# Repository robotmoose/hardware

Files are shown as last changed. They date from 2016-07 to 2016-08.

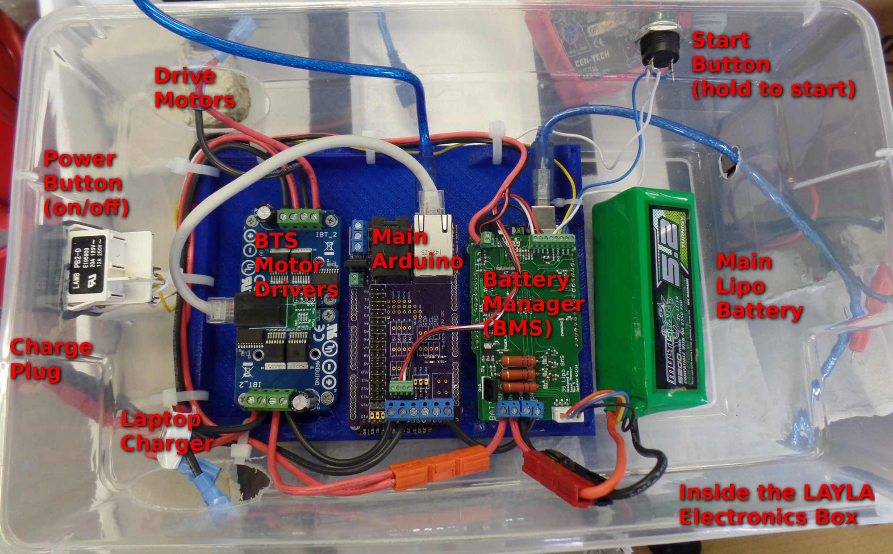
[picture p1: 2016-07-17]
layla/hardware/layla_electronics_box.jpg

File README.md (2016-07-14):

# RobotMoose Web Robotics System Hardware



Several robotics platforms are being developed specifically for use with the RobotMoose Web Robotics System. This repository stores files related to the hardware developed for these systems.
* The **layla**, **quizbot**, and **roomba** folders contain firmware and 3d models of parts and assemblies for those respective systems.
* The **sensors** folder contains files for subsystems being developed to expand the functionality of our robotics platforms.

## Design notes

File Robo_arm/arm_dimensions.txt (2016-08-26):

//Arm dimensions

//from shoulder/ball joint to forearm
first length = 8 inches or (8in*2.5cm = 20cm)   215mm 

//forearm
9 inches or (9in * 2.5cm = 22.5cm) 200mm

//wrist

//finger
2inches on each side of the corner or 4 inches total = 5cm = 50mm

35mm for bottom 
50mm for top including tip
30mm w/o tip

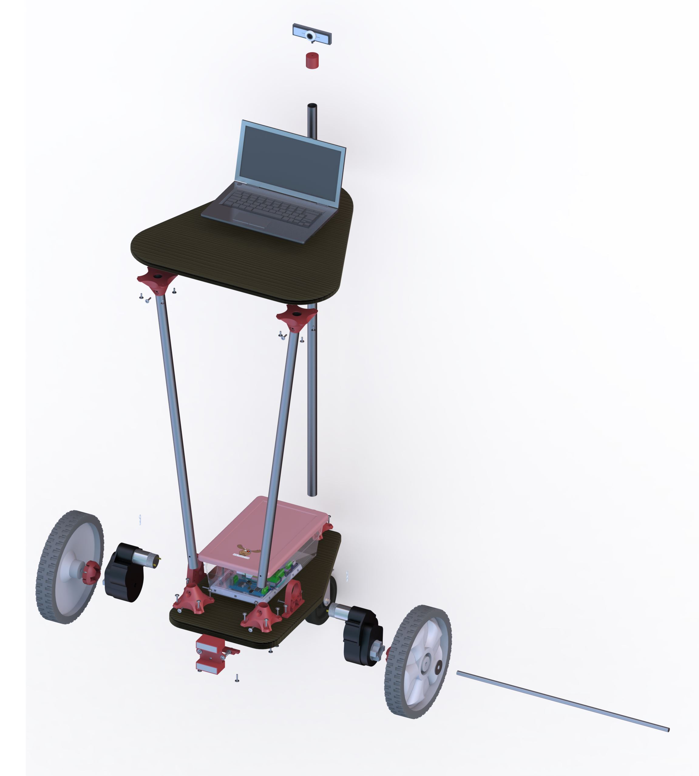
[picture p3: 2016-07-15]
layla/SolidWorks/Renders, Animations, & Schematics/Layla_Exploded_Isometric.jpg

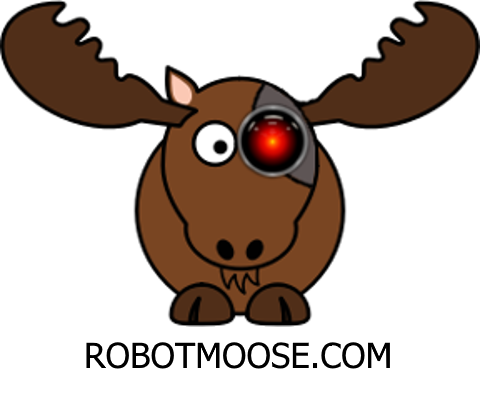
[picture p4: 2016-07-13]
layla/SolidWorks/electronics_box/moose_sticker.png

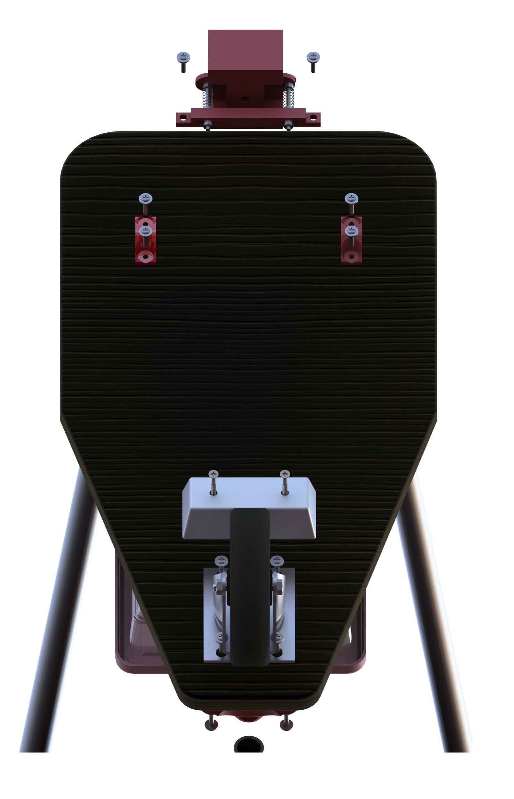
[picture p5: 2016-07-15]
layla/SolidWorks/Renders, Animations, & Schematics/Layla_Explode_Bottom.jpg

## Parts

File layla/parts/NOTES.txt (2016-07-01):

Bottom plywood: 
	3/4 inch thick
	10 inches wide
	22 inches deep
	
Top plywood: 
	5mm thick, approx
	22 inches wide (must be as wide as wheels, to make driving easier)
	22 inches deep
	Work surface sits 38 inches off the ground

Electrical Metallic Tubing (EMT), 3/4 inch (nominal), 23.5mm (actual)
	1x 44 inch long upright for camera
	2x 32 inch long slanted uprights; slant angle is 11 degrees from vertical

Axle:
	22.75 inch 3/8" (or 7/16" if available) steel axle; both ends cross-drilled for retaining clips.

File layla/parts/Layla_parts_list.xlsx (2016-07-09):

part # | part | dimension | quantity | source | price
965207 | drive wheel | 11in | 2 | home depot | $21.98
235574 | caster wheel |  | 1 | lowes | $11.97
90075K145 | axle | 7/16 x ? |  | mcmaster | $7.01
SAGI9951KWN | motor/gears |  | 1 | tiger imports | $22.00
154280 | plywood base | 20" x 12" | 1 | lowes | $14.93
154277 | plywood top | 22" x 22" | 1 | lowes | $13.27
 | electronics tray |  | 1 | RobotMoose | $91.16
16428012 | shoe box |  | 1* | walmart | $8.69
B00JTBMD7E | Arduino Mega |  | 1* | amazon | $18.99
B008GRTSV6 | Arduino Uno |  | 1* | amazon | $15.99
B00WSN98DC | BTS7960 Motor control |  | 1* | amazon | $13.59
912700001-0 | Battery | 3S 5.2aH | 1* | hobby king | $16.99
 | BMS UNO shield |  | 1* | RobotMoose | $74.25
 | Mainboard Mega Shield |  | 1* | RobotMoose | $165.41
 | BTS dual adapter |  | 1* | RobotMoose
B00852KMLC | LAN cable | 12" | 1* | amazon | $4.98
B00NH11KIK | usb cable | 6' | 1* | amazon | $4.99
B00NAY1T80 | start button |  | 1* | amazon | $5.99
PB241D212Z02T-ND | E-stop Button |  | 1* | digikey | $2.75
72713 | Metal upright legs |  | 1 | lowes | $3.99
 | printed wheel adapters |  |  | robotMoose download | $22.70
 | printed rear volcanoes |  |  | robotMoose download
 | printed front volcanoes |  |  | robotMoose download
 | printed webcam holder |  |  | robotMoose download
B00GZB8D0M | laptop |  | 1 | amazon | $139.29
B0080CE5M4 | webcam |  | 1 | amazon | $30.69
205142852 | volcano-base screw | #8 x 3/4 | partial box | home depot | $5.64
205142871 | volcano-top screw | #8 x 1/2 | partial box | home depot | $5.64
122235 | leg screws |  | partial box | lowes | $6.14
 |  |  |  |  | $751.01
*included with electronics box
download link:
https://github.com/robotmoose/robotmoose/tree/master/layla/parts

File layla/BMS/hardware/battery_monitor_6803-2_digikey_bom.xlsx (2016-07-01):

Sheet: Sheet1
Qty | Value | Package | Reference | digikey #
3 |  | LED-0603 | LED1, LED2, LED3 | 475-2512-1-ND
3 | 0.1uF | 0603-CAP | C1, C2, C3 | 490-1532-1-ND
5 | 100 | 0603-RES | R4, R5, R6, R7, R8 | RHM100CGCT-ND
1 | 100k | 0603-RES | R11 | RHM100KCGCT-ND
3 | 1Meg | 0603-RES | R22, R23, R24 | RHM1MCGCT-ND
4 | 1uF | 0603-CAP | C4, C5, C6, C7 | 490-10487-1-ND
3 | 3.3k | 0603-RES | R1, R2, R3 | RHM3.3KCGCT-ND
10 | 4.7k | 0603-RES | R9, R10, R12, R13, R14, R15, R19, R20, R21, R25 | RHM4.7KCGCT-ND
3 | 470 | 0603-RES | R16, R17, R18 | RHM470CGCT-ND
1 | LTC6803-2 | FSOP-44 | U$5 | LTC6803IG-2#PBF-ND
4 | MOSFET-NCHANNELBSS138 | SOT23 | Q2, Q6, Q7, Q8 | SSM3K333RLF(TCT-ND
4 | MOSFET-PCHANNELIRLML2244 | SOT23-3 | Q1, Q3, Q4, Q5 | SSM3J334RLFCT-ND
3 | PDZ7.5B | SOD-323 | DZ1, DZ2, DZ3 | MM3Z7V5ST1GOSCT-ND
1 | PMLL41SOD80C | SOD80C | D2 | LS4148-GS18CT-ND
1 | PMOS_AO4435 | SOIC8 | Q9 | BSO613SPV GCT-ND
3 | RESISTOR-POWER-3W | RESISTOR-3W | U$1, U$2, U$3 | PPC20W-3JTB-ND
2 | SCREW_TERMINAL_2 | SCREW_TERMINAL_2 | I2C, RELAYS, THERM | A98333-ND
1 | SCREW_TERMINAL_3 | SCREW_TERMINAL_3 | U$4 | A98334-ND
1 |  | through-hole | cell connector | 455-2237-ND

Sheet: battery_monitor_6803-2
Qty;"Value";"Device";"Package";"Parts";"Description";"PROD_ID";"VALUE";
3;"";"LED0603";"LED-0603";"LED1 | LED2 | LED3";"LEDs";"";"";
5;"";"SOLDERJUMPER_2WAYS";"SJ_3";"A0 | A1 | A2 | A3 | TOS";"Solder Jumper";"";"";
3;"0.1uF";"0.1UF-100V-10%(0603)";"0603-CAP";"C1 | C2 | C3";"CAP-08390";"CAP-08390";"0.1uF";
5;"100";"3.3KOHM1/10W1%(0603)";"0603-RES";"R4 | R5 | R6 | R7 | R8";"RES-07851";"RES-07851";"";
1;"100k";"3.3KOHM1/10W1%(0603)";"0603-RES";"R11";"RES-07851";"RES-07851";"";
3;"1Meg";"3.3KOHM1/10W1%(0603)";"0603-RES";"R22 | R23 | R24";"RES-07851";"RES-07851";"";
4;"1uF";"0.1UF-100V-10%(0603)";"0603-CAP";"C4 | C5 | C6 | C7";"CAP-08390";"CAP-08390";"0.1uF";
3;"3.3k";"3.3KOHM1/10W1%(0603)";"0603-RES";"R1 | R2 | R3";"RES-07851";"RES-07851";"";
10;"4.7k";"3.3KOHM1/10W1%(0603)";"0603-RES";"R9 | R10 | R12 | R13 | R14 | R15 | R19 | R20 | R21 | R25";"RES-07851";"RES-07851";"";
3;"470";"3.3KOHM1/10W1%(0603)";"0603-RES";"R16 | R17 | R18";"RES-07851";"RES-07851";"";
1;"ARDUINO_R3_SHIELD";"ARDUINO_R3_SHIELD";"UNO_R3_SHIELD";"U$8";"Shield form compatible with the Arduino Uno R3.";"";"";
1;"LTC6803-2";"LTC6803-2";"FSOP-44";"U$5";"";"";"";
4;"MOSFET-NCHANNELBSS138";"MOSFET-NCHANNELBSS138";"SOT23";"Q2 | Q6 | Q7 | Q8";"Common NMOSFET Parts";"TRANS-00830";"";
4;"MOSFET-PCHANNELIRLML2244";"MOSFET-PCHANNELIRLML2244";"SOT23-3";"Q1 | Q3 | Q4 | Q5";"Generic PMOSFET";"TRANS-11153";"";
3;"PDZ7.5B";"DIODE-ZENER-BZT52";"SOD-323";"DZ1 | DZ2 | DZ3";"Zener Diode";"";"";
1;"PMLL41SOD80C";"PMLL41SOD80C";"SOD80C";"D2";"High-speed diodes";"";"";
1;"PMOS_AO4435";"PMOS_AO4435";"SOIC8";"Q9";"";"";"";
3;"RESISTOR-POWER-3W";"RESISTOR-POWER-3W";"RESISTOR-3W";"U$1 | U$2 | U$3";"PR03 series .205" dia x .657" L";"";"";
3;"SCREW_TERMINAL_2";"SCREW_TERMINAL_2";"SCREW_TERMINAL_2";"I2C | RELAYS | THERM";"";"";"";
2;"SCREW_TERMINAL_4";"SCREW_TERMINAL_4";"SCREW_TERMINAL_4";"CELL_CONNECTION | U$4";"";"";"";

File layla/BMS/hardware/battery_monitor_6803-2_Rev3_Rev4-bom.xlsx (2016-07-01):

Order list for /home/clayauld/Documents/Seafile/UAF/ITEST/ITEST Eagle/BMS/battery_monitor_6803-2_Rev4.sch
Exported from EAGLE with DesignLink
Parts for 3 boards
Quantity | Value | Package | Newark Order code | Digikey order code | Manufacturer | Manuf. Code | Reference | Availability | Price (from) | Description
9 | 0.1uF | 0603-CAP | 01H6821 | 490-1532-1-ND | AVX CORPORATION | 0603YG104ZAT2A | C1, C2, C3 | 48000 | 0.016 | AVX - 0603YG104ZAT2A - CAPACITOR | CERAMIC | 0.1UF | 16V | Y5V | 80% |  | -20% | 603 | FULL REEL
12 | 1uF | 0603-CAP | 04X3184 | 490-10487-1-ND |  | C0603X5R0J105M030BC | C4, C5, C6, C7 | 35812 | 0.086 | TDK - C0603X5R0J105M030BC - CERAMIC CAPACITOR | 1UF | 6.3V | X5R | 201
3 | SCREW_TERMINAL_4 | SCREW_TERMINAL_4 | 12H8388 | A98335-ND | TYCO ELECTRONICS | 282834-4 | Charger/Battery+ | 5317 | 1.02 | TE CONNECTIVITY / BUCHANAN - 282834-4 - TERMINAL BLOCK | PCB | 4 POSITION | 30-16AWG
3 | PMLL41SOD80C | SOD80C | 18C6408 | LS4148-GS18CT-ND | FAIRCHILD SEMICONDUCTOR | FDLL4148 | D2 | 8482 | 0.015 | FAIRCHILD SEMICONDUCTOR - FDLL4148 - SMALL SIGNAL DIODE 100V 200mA LL-34
9 | PDZ7.5B | SOD-323 | 04X4941 | MM3Z7V5ST1GOSCT-ND |  | PDZ7.5B | DZ1, DZ2, DZ3 | 115 | 224 | 0.021 | NXP - PDZ7.5B | 115 - DIODE | ZENER | 7.5V | 400MW | SOD-323-2
9 | SCREW_TERMINAL_2 | SCREW_TERMINAL_2 | 12H8386 | A98333-ND | TYCO ELECTRONICS | 282834-2 | I2C, ESTOP, THERM | 2599 | 0.502 | TE CONNECTIVITY / BUCHANAN - 282834-2 - TERMINAL BLOCK | PCB | 2 POSITION | 30-16AWG
9 |  | LED-0603 | 95W3795 | 732-4978-1-ND |  | 150060RS75000 | LED1, LED2, LED3 | 20 | 0.101 | WURTH ELEKTRONIK - 150060RS75000 - LED | 603 | RED | 250MCD | 625NM
12 | MOSFET-PCHANNELIRLML2244 | SOT23-3 | 40X8697 | SSM3J334RLFCT-ND |  | SI2369DS-T1-GE3 | Q1, Q3, Q4, Q5 | 0 | 0.126 | VISHAY SILICONIX - SI2369DS-T1-GE3 - MOSFET | P CH | -30V | -7.6A | SOT-23-3
12 | MOSFET-NCHANNELBSS138 | SOT23 | 52R2613 | SSM3K333RLF(TCT-ND |  | IRLML0030TRPBF | Q2, Q6, Q7, Q8 | 2952 | 0.169 | INTERNATIONAL RECTIFIER - IRLML0030TRPBF - N CHANNEL MOSFET | 30V | 5.3A | SOT-23
3 | PMOS_AO4435 | SOIC8 | 16P3885 | BSO613SPV GCT-ND |  | SI9407BDY-T1-GE3 | Q9 | 1742 | 0.56 | VISHAY SILICONIX - SI9407BDY-T1-GE3 - P CHANNEL MOSFET | -60V | 4.7A | SOIC
3 | IRF9530 | TO220BV | 14T4215 | 497-2729-5-ND |  | NTE2383 | Q10 | 64 | 8.61 | NTE ELECTRONICS - NTE2383 - MOSFET | P CHANNEL | 100V | 10.5A | TO-220-3
9 | 3.3k | 0603-RES | 52K8368 | RHM3.3KCGCT-ND | VISHAY/DALE | CRCW06033K00FKEA | R1, R2, R3 | 3110 | 0.009 | VISHAY DALE - CRCW06033K00FKEA - THICK FILM RESISTOR | 3KOHM | 100mW | 1%
15 | 100 | 0603-RES | 05X8794 | RHM100CGCT-ND |  | ERJ-1GNF1000C | R4, R5, R6, R7, R8 | 20035 | 0.008 | PANASONIC ELECTRONIC COMPONENTS - ERJ-1GNF1000C - THICK FILM RESISTOR | 100 OHM | 1% | 201
30 | 4.7k | 0603-RES | 52K8494 | RHM4.7KCGCT-ND | VISHAY/DALE | CRCW06034K70FKEA | R9, R10, R12, R13, R14, R15, R19, R20, R21, R25 | 6964 | 0.003 | VISHAY DALE - CRCW06034K70FKEA - THICK FILM RESISTOR | 4.7KOHM | 100mW | 1%
3 | 100k | 0603-RES | 39K0075 | RHM100KCGCT-ND | FARNELL | MC0063W06035100K | R11 | 4003 | 0.011 | MULTICOMP - MC0063W06035100K - THICK FILM RESISTOR | 100KOHM | 63mW | 5%
9 | 470 | 0603-RES | 05X8640 | RHM470CGCT-ND |  | ERJ-P03F4700V | R16, R17, R18 | 4890 | 0.071 | PANASONIC ELECTRONIC COMPONENTS - ERJ-P03F4700V - THICK FILM RESISTOR | 470 OHM | 1% | 603
12 | 1Meg | 0603-RES | 64R5311 | RHM1MCGCT-ND |  | ERJ-3EKF1004V | R22, R23, R24, R26 | 2513 | 0.003 | PANASONIC ELECTRONIC COMPONENTS - ERJ-3EKF1004V - THICK FILM RESISTOR | 1MOHM | 100mW | 1%
9 | RESISTOR-POWER-3W | RESISTOR-3W | 52W7905 | PPC20W-3JCT-ND |  | ERG-3SJ200 | U$1, U$2, U$3 | 1214 | 0.099 | PANASONIC ELECTRONIC COMPONENTS - ERG-3SJ200 - RESISTOR | 20 OHM | 3W | 5% | AXIAL
3 | LTC6803-2 | FSOP-44 | unknown | LTC6803IG-2#PBF-ND |  |  | U$5 |  |  |  |  |  |  |  |  | 1 | LTC6803-2 | FSOP-44 | unknown | LTC6803IG-2#PBF-ND
3 | TACTILE-SWITCH-7914G | 7914G | 05B2757 | 7914G-000ECT-ND | BOURNS | INC. | U$7 | 7914G-1-000E | 338 | 0.465 | BOURNS - 7914G-1-000E - PUSHBUTTON | SPST-NO | 100MA | SMDGULLWING
3 | 3 cell jst connector | Jst-3-cell | 37K9958 | 455-2237-ND |  |  | Cell connection

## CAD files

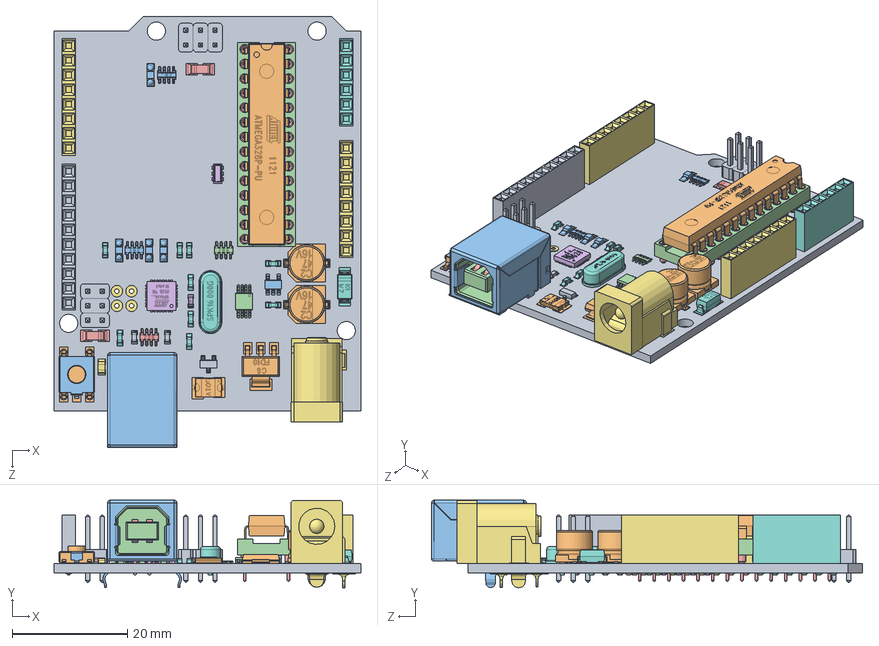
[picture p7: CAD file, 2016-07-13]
layla/SolidWorks/electronics_box/arduino uno.SLDASM
53.3 x 15.2 x 74.9 mm
unoboard blue
47uf CAP Dcase x 2
USB SHELL
USB core
usb top contact x 2
usb btm contact x 2
power jack
crystal
2pin_header__02 x 6
nano - reg
led x 4
dip28
dip socket pin x 28
atmega16u2
8 PORT HEADER x 2
6 PORT HEADER
10 PORT HEADER
ATMEL328P
102 RESISTOR PACK x 2
103 RESISTOR PACK
220 RESISTOR PACK
16mhz crystal - measured
PADS001
603 cap on pad x 9
ssot3
mf-msmf050-2
lmv358
lp2985dgkr
cd1206 diode x 2
603 resistor
blm21
m7 diode
MLC0603 x 2
RESET CORE
RESET

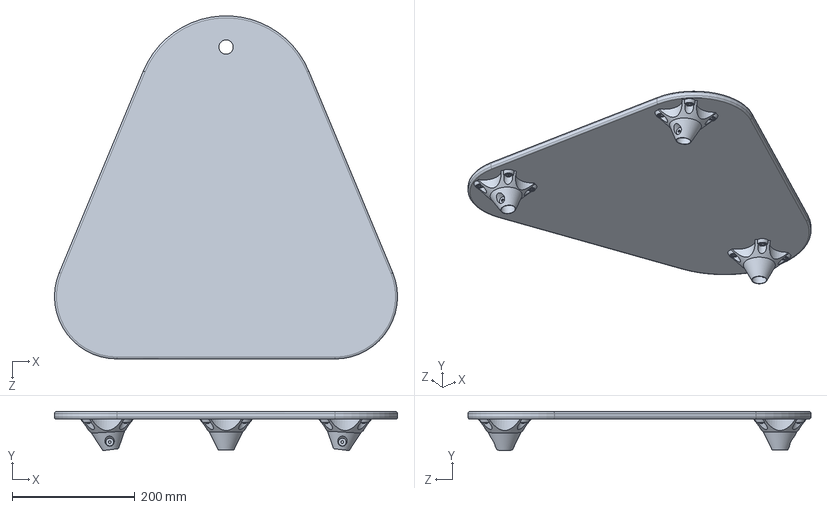
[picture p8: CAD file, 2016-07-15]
layla/SolidWorks/Layla_Top_Full.SLDPRT
558.8 x 63.9 x 558.6 mm

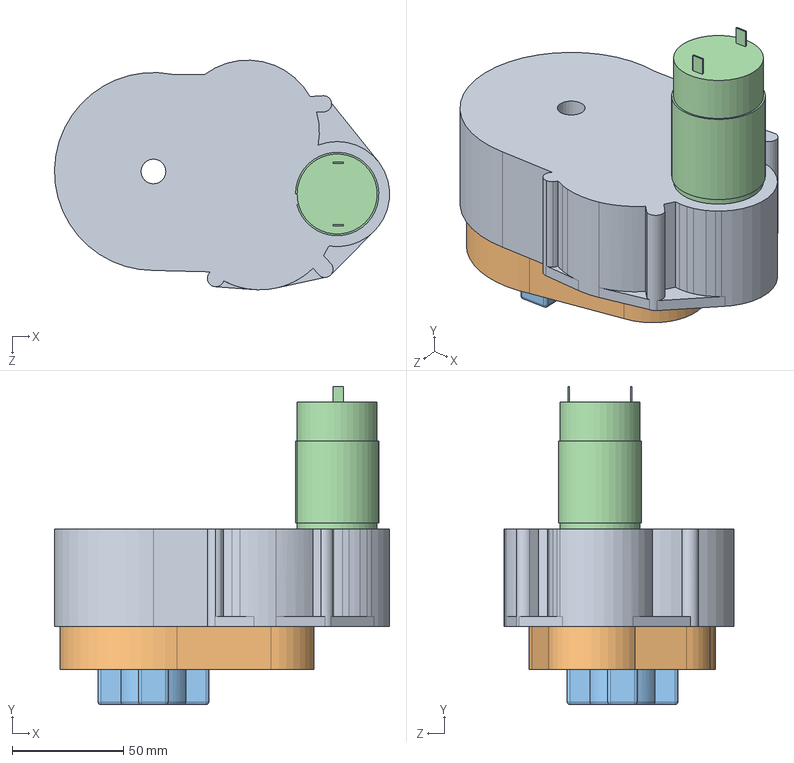
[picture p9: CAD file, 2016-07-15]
layla/SolidWorks/Peg_Perego_Gearbox/Peg_Perego_Gearbox.SLDASM
150.5 x 143.0 x 103.1 mm
Peg_Perego_Gearbox_Bottom
Peg_Perego_Gearbox_Top
Peg_Perego_Gearbox_Big_Gear
Peg_Perego_Gearbox_Motor

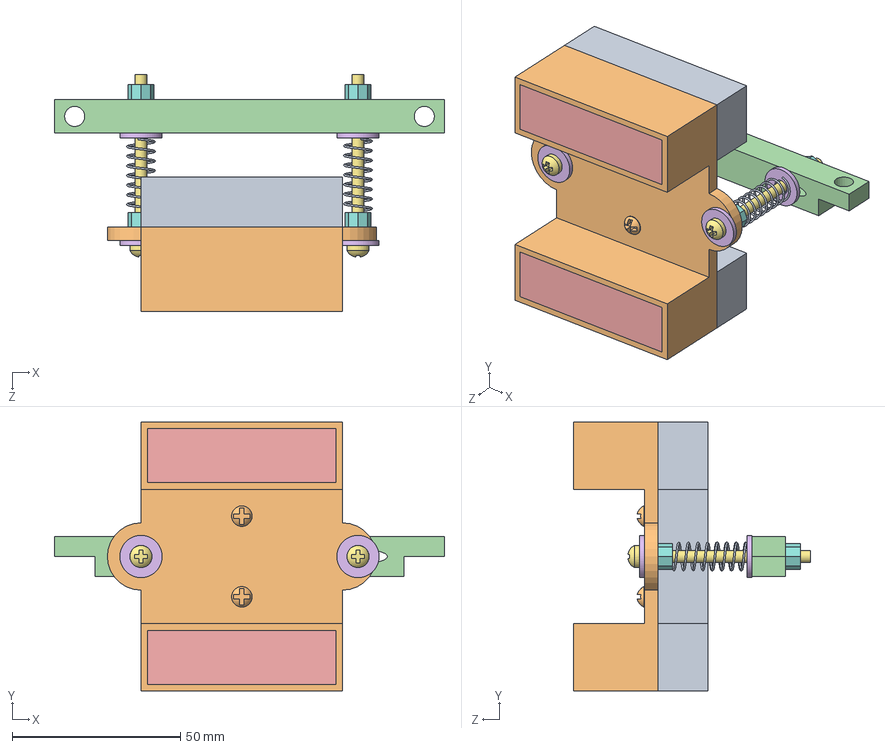
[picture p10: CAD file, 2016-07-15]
layla/SolidWorks/Charger/Charger.SLDASM
116.0 x 80.0 x 70.4 mm
Charger_Back
Charger_Front_1
Charger_Front_2 x 2
Charge_Bracket
Charge_Plate x 2
Charger_Washer_10 x 4
Charger_Bolt_6_(2.0'') x 2
Charger_Nut_6 x 4
Charger_Spring x 2
Charger_Bolt_Small x 2

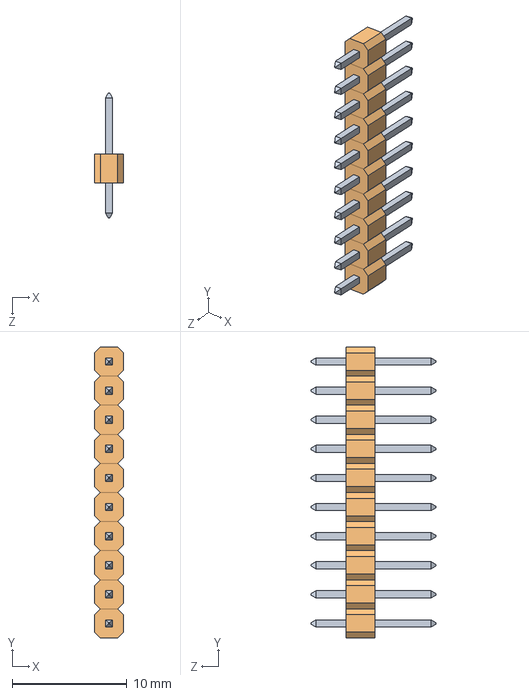
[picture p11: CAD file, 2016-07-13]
layla/SolidWorks/electronics_box/header_male_1x10.SLDASM
2.54 x 25.4 x 10.9 mm
header_pin x 10
header_pin_base_single x 10

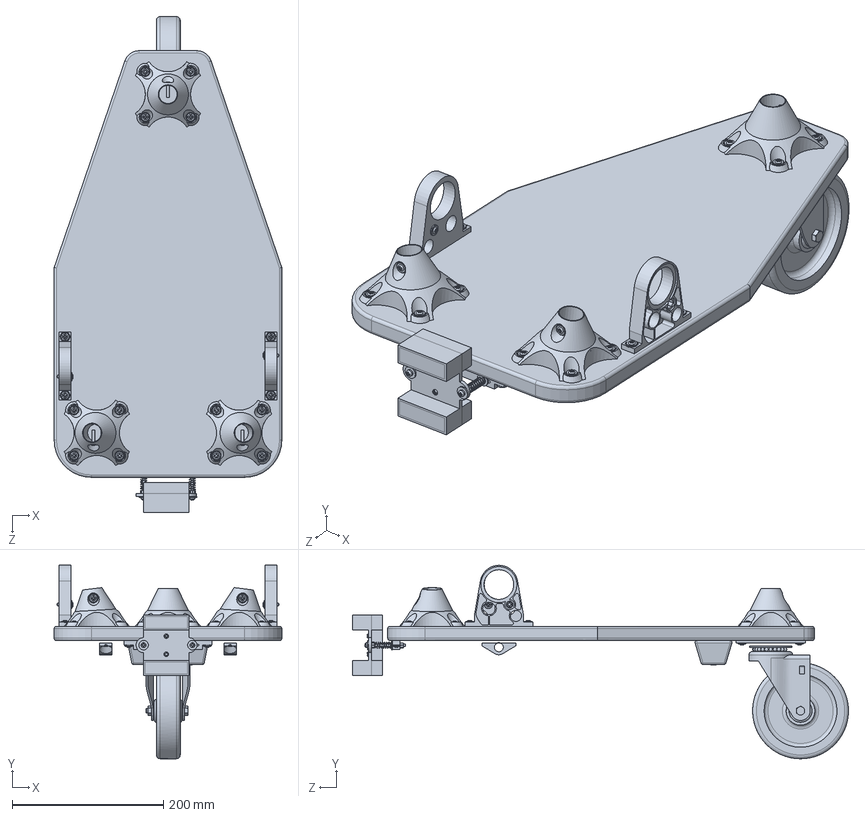
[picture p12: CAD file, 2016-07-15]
layla/SolidWorks/Layla_Bottom_Full.SLDPRT
301.6 x 256.3 x 656.9 mm

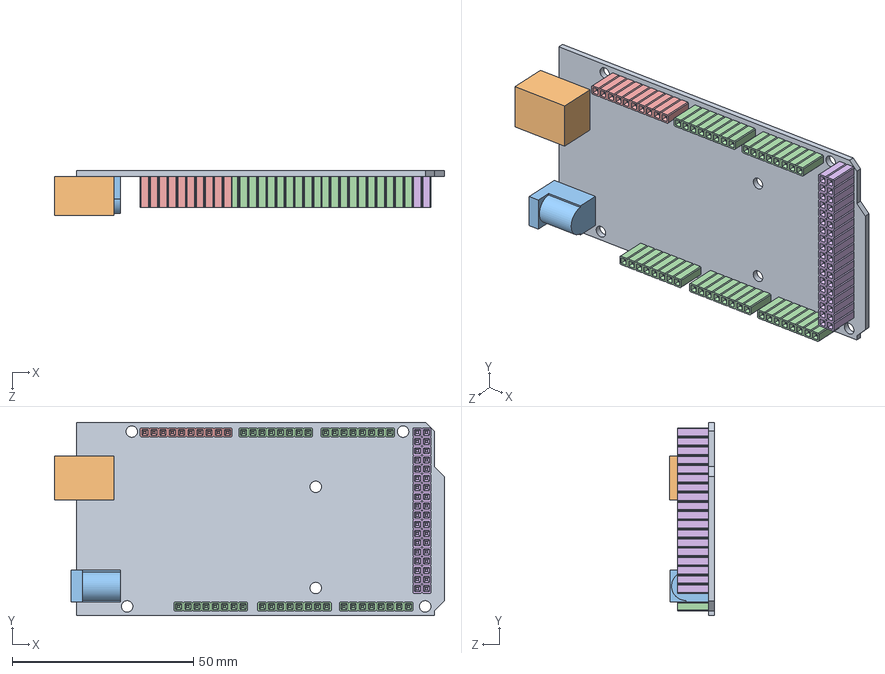
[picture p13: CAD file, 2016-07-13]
layla/SolidWorks/electronics_box/Arduino_mega.SLDASM
107.7 x 53.3 x 12.4 mm
Arduino_mega
USB-jack
DC-jack
header_8-pin x 5
header_10-pin
header_36-pin

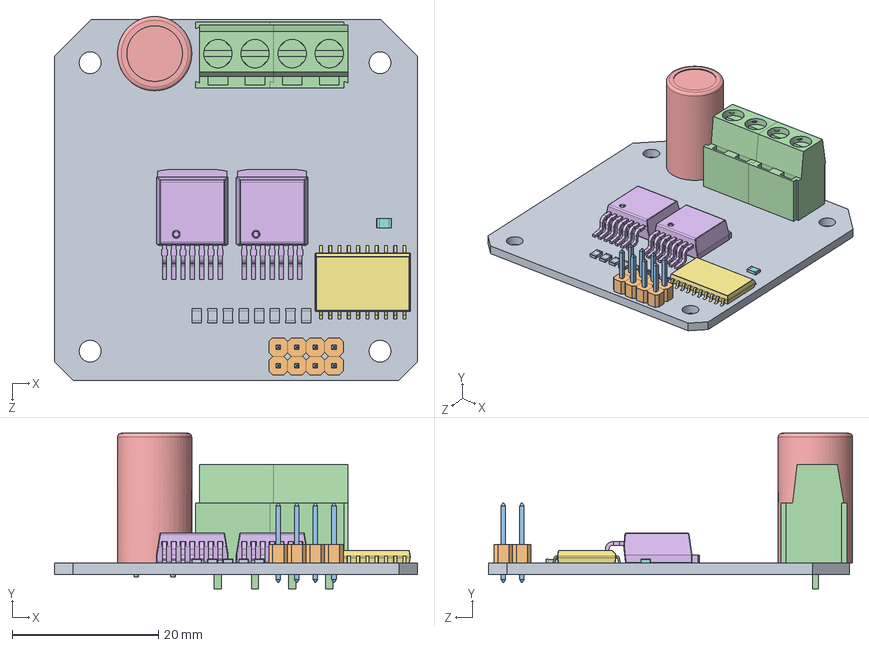
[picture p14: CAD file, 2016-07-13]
layla/SolidWorks/electronics_box/ibt2_assembly.SLDASM
49.7 x 21.3 x 49.8 mm
IBT2_pcb
header_pin_base_2x4
header_pin x 8
AMP_screw-terminal_2POS_large x 2
cap_5mm_pitch
d2pak x 2
SOIC20 wide
cap_0805
resistor_0805 x 8

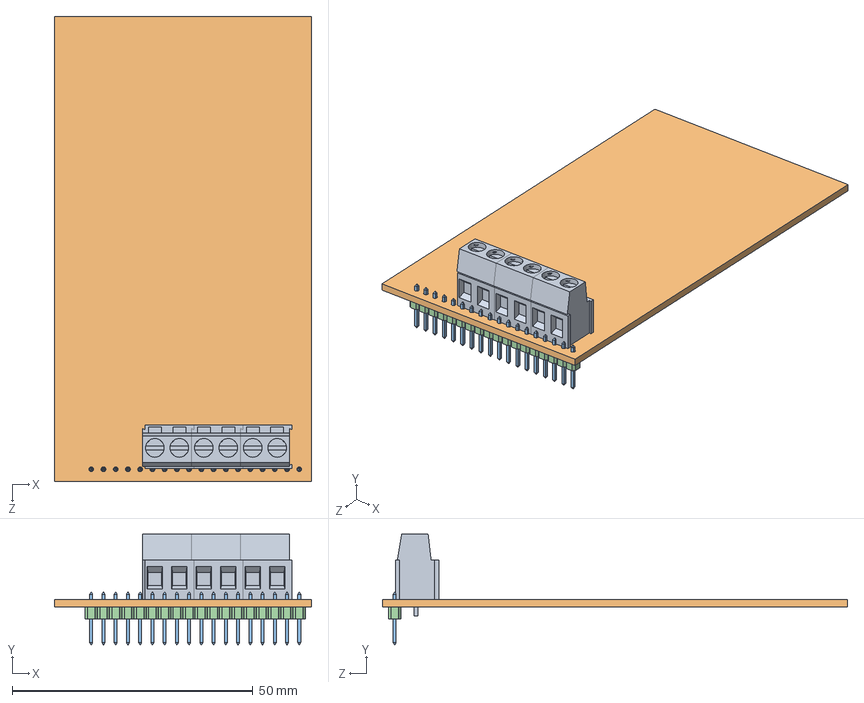
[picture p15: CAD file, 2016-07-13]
layla/SolidWorks/electronics_box/mainboard_assembly.SLDASM
53.3 x 22.9 x 96.5 mm
AMP_screw-terminal_2POS_large x 3
mainboard_pcb
header_pin x 18
header_pin_base_single x 18

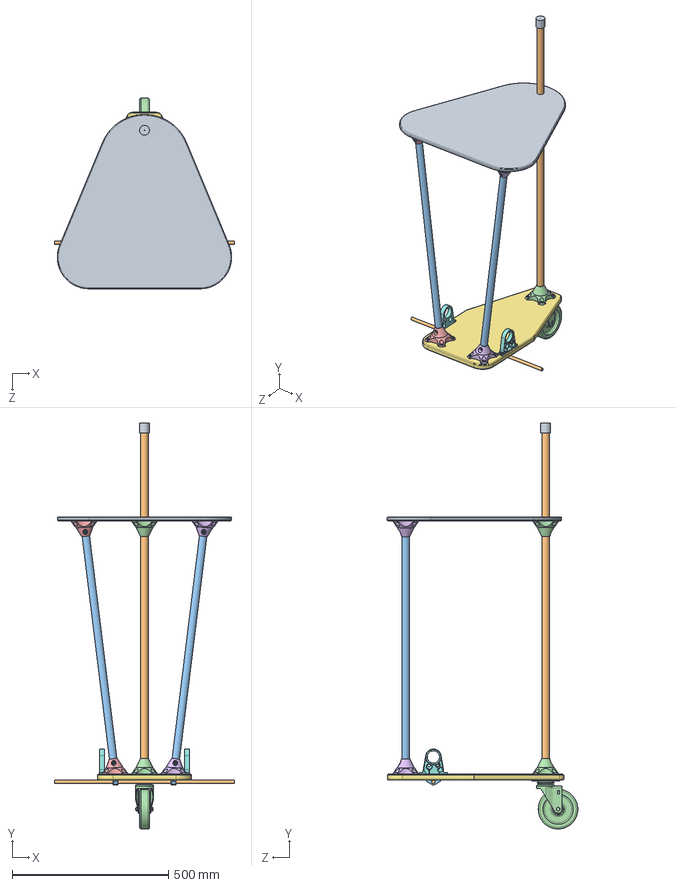
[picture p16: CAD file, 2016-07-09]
layla/SolidWorks/Layla.SLDASM
577.9 x 1300.7 x 611.1 mm
Layla_Top
Conduit_Back
Conduit_Front x 2
frame_bracket_volcano_back x 2
Volcano_Left_7 x 2
Volcano_Right_7 x 2
Layla_Bottom
motor_bracket x 2
Camera_Bracket
Axle_7_16
axle_bracket_7_16 x 2
Caster Part
SCREW_8-FH(0.750'') x 26
SCREW_8-FH(0.500'') x 12

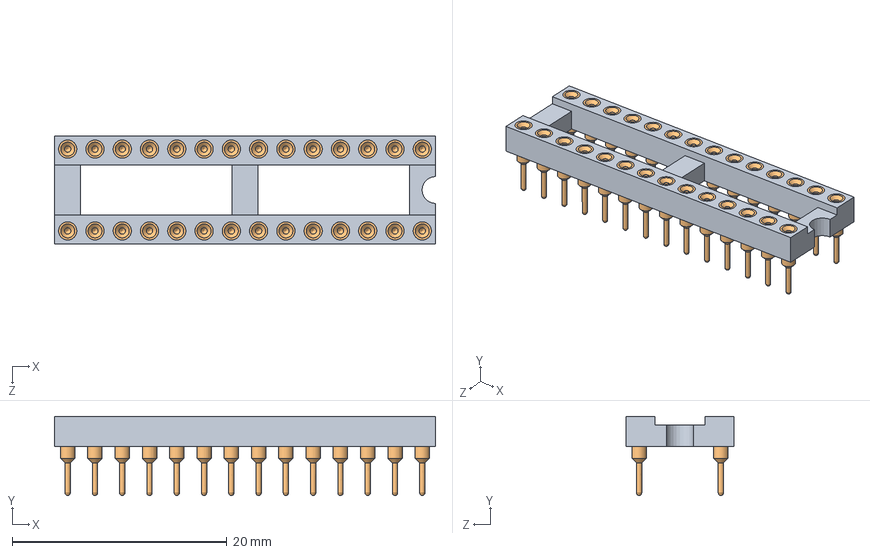
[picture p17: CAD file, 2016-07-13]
layla/SolidWorks/electronics_box/dip28.SLDASM
35.5 x 7.37 x 10.1 mm
dip28
dip socket pin x 28

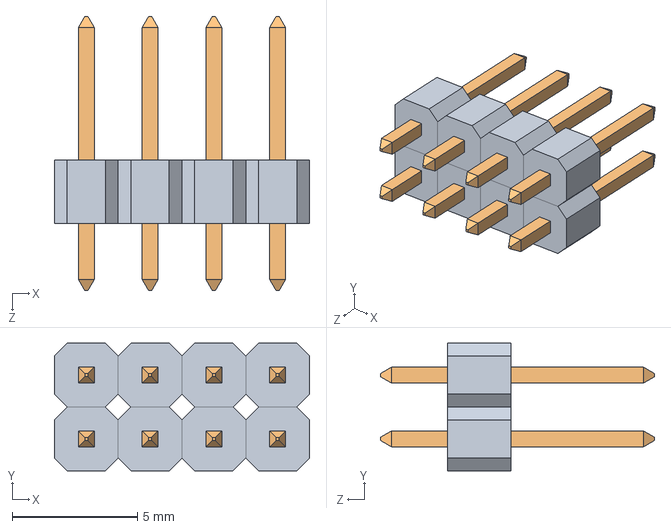
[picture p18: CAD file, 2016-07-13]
layla/SolidWorks/electronics_box/header_male_2x4.SLDASM
10.2 x 5.08 x 10.9 mm
header_pin_base_2x4
header_pin x 8

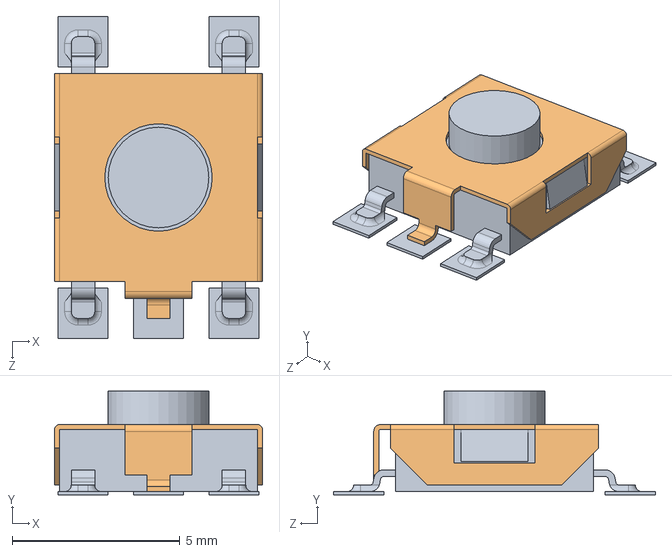
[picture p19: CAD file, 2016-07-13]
layla/SolidWorks/electronics_box/RESET BUTTON.SLDASM
6.20 x 3.10 x 9.60 mm
RESET CORE
RESET

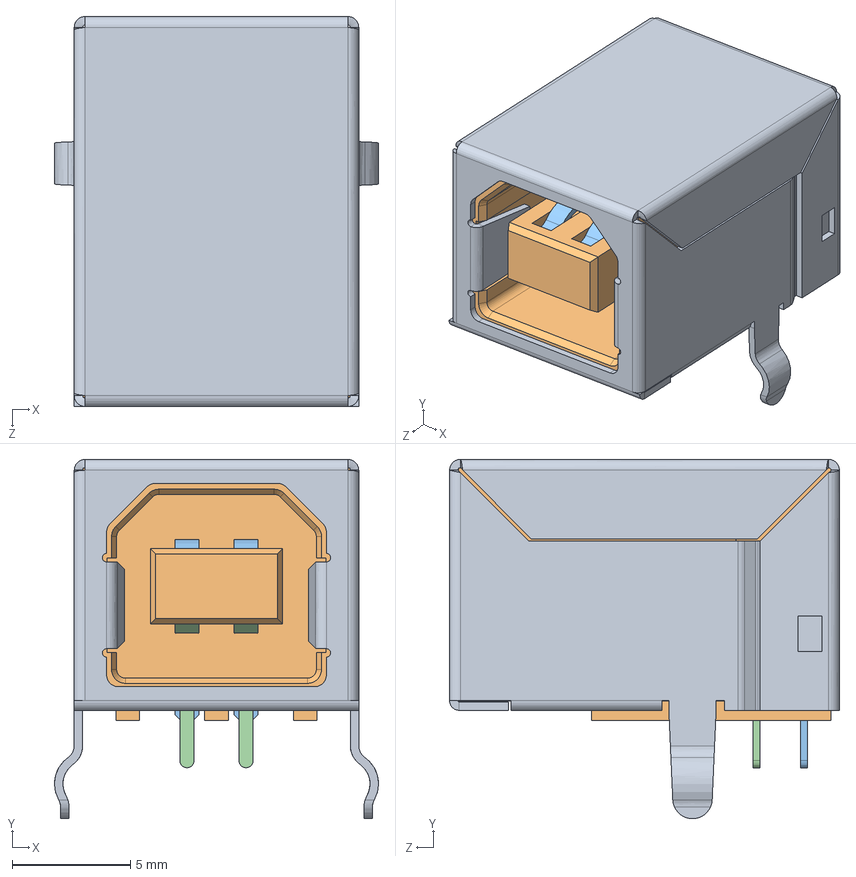
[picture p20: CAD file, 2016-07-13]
layla/SolidWorks/electronics_box/USB type b.SLDPRT.SLDASM
13.7 x 15.2 x 16.5 mm
USB SHELL
USB core
usb top contact x 2
usb btm contact x 2

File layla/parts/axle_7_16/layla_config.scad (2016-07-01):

// Main parameters used for most Layla parts
$fa=15;
$fs=0.1;

// This number avoids roundoff problems
epsilon=0.02;

// This is how much your printer squishes extra around holes
//   bigger value leaves more space for globs.
clearance=0.3;

// Removeable parts leave this much extra diameter
wiggle=0.1;

// Wall thickness for most parts--two nozzle diameters typ.
wall=0.8;

// Floor thickness--at least 4 layers
floor=1.2;


// This is the main drive axle
axle_dia=7/16*25.4+2*clearance+wiggle;

// Main frame tubing
tube_OD=23.5+2*clearance;


// Main woodscrews: Everbilt #8x9/16" lath screws
woodscrew_head_dia=12.5;
woodscrew_shaft_OD=4.5;
woodscrew_shaft_ID=3.0;
woodscrew_shaft_len=20.0;
woodscrew_boss=1.0; // extra thickness under screw head

// Clearance for woodscrew to pass through (minus)
module woodscrew_head(head_clear_scale=1.0) 
{
    head_clear=0.5*floor+epsilon+head_clear_scale*10;
    translate([0,0,woodscrew_boss]) {
        // Head clearance
        cylinder(d1=woodscrew_head_dia,d2=woodscrew_head_dia+0.7*head_clear,h=head_clear);
        
        // Through clearance for shaft of screw
        translate([0,0,+epsilon])
        scale([1,1,-1])
            cylinder(d=woodscrew_shaft_OD,h=woodscrew_shaft_len);
    }
}

// Raised area reinforcing woodscrew (plus)
module woodscrew_boss()
{
    boss_ht=1.5*floor+woodscrew_boss;
    translate([0,0,-floor])
        cylinder(d1=woodscrew_head_dia*1.8,d2=woodscrew_head_dia*1.3,h=boss_ht);
}

/*
difference() {
    woodscrew_boss();
    woodscrew_head();
}
*/

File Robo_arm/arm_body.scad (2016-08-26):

//arm_body.scad
//Laurin Fisher
//Makes the holding for the servos along the arm, the arm itself. Units are in Milimeters. 

error = 0.5; 
$fn = 30; 

//The wrist dimensions
side_wall_depth = 6 + error; 

wrist_width = 41 + side_wall_depth*2 + error; 
wrist_length = 48 + side_wall_depth*2 + error; 
wrist_height = wrist_width; 

//Servo dimensions
servo_width = 41 + error; 
servo_length = 20 + error; 

difference(){
union(){
difference(){
union(){
difference(){
union(){ 
difference(){
//Make the cube/holding 
translate([-wrist_width/2, -wrist_length/2, 0])
    cube([wrist_width, wrist_length, wrist_height]); 

//Cut out the sides and middle of the cube for lightness
union(){
translate([-(wrist_width-side_wall_depth*2)/2,-(wrist_length-side_wall_depth*2)/2, -1])
    cube([wrist_width-side_wall_depth*2, wrist_length-side_wall_depth*2, 100]); //100 = arbitrary big number
    
translate([-50,-(wrist_length-side_wall_depth*2)/2, side_wall_depth])
    cube([100, wrist_length-side_wall_depth*2, wrist_height-side_wall_depth*2]); 
}
}
}

translate([-servo_width/2, -servo_length/2 + wrist_length/2, -side_wall_depth + wrist_height/2])
    cube([servo_width, servo_length, side_wall_depth*2]); 
}

//Make the side opening for the bottom servo
side_wall_servo_hole_y = -wrist_length/2 + side_wall_depth + servo_length; 
translate([-side_wall_depth/2 + wrist_width/2 -error*6.5, -side_wall_depth/2 + side_wall_servo_hole_y , 0])
    cube([side_wall_depth, side_wall_depth, wrist_height]); 

//Make the supports
//Bottom side 

translate([-wrist_width/2+side_wall_depth/2, -wrist_height/2+ side_wall_depth/2, 0])
rotate([0,0,-40])
    cube([side_wall_depth, wrist_height + side_wall_depth*2, side_wall_depth]);

//Top Side

translate([-wrist_width/2+side_wall_depth/2, -wrist_height/2+ side_wall_depth/2, wrist_height-side_wall_depth])
rotate([0,0,-40])
    cube([side_wall_depth, wrist_height + side_wall_depth*2, side_wall_depth]);
    
//Side w/ Servo
rotate([60,0,0])
translate([wrist_width/2-side_wall_depth, 0, 0])
    cube([side_wall_depth, wrist_height, side_wall_depth]); 
    

translate([wrist_width/2-side_wall_depth, -side_wall_depth/2, wrist_height-side_wall_depth])
rotate([-60,0,0])
    cube([side_wall_depth, wrist_height, side_wall_depth]);
}

//Make the bottom opening for the wires
wire_cube_size = 13 + error; 
translate([-wire_cube_size/2, -wire_cube_size/2 - wrist_length/2, -wire_cube_size/2 + wrist_height/2])
cube([wire_cube_size,wire_cube_size,wire_cube_size]); 


//Make the opening for the pegs on the left side
rad_error = 0.1; 
//Bottom Right when facing side
translate([-wrist_width/2 - side_wall_depth/4, -wrist_length/2 + side_wall_depth/2, side_wall_depth/2])
rotate([0,90,0])
cylinder(side_wall_depth/2, 1+rad_error, 1+rad_error); 

//Top Right
translate([-wrist_width/2 - side_wall_depth/4, -wrist_length/2 + side_wall_depth/2, wrist_height-side_wall_depth/2])
rotate([0,90,0])
cylinder(side_wall_depth/2, 1+rad_error, 1+rad_error); 

//Top Left
translate([-wrist_width/2 - side_wall_depth/4, wrist_length/2 - side_wall_depth/2, wrist_height-side_wall_depth/2])
rotate([0,90,0])
cylinder(side_wall_depth/2, 1+rad_error, 1+rad_error); 

//Bottom Left
translate([-wrist_width/2 - side_wall_depth/4, wrist_length/2 - side_wall_depth/2, side_wall_depth/2])
rotate([0,90,0])
cylinder(side_wall_depth/2, 1+rad_error, 1+rad_error); 


}
}
/*
// TOP OF THE WRIST BOX
translate([-wrist_width, -wrist_length, -side_wall_depth])
cube([wrist_width*2, wrist_length*2, wrist_height]); 

//Make the pegs
rad_error = 0.1; 
//Top Right
translate([wrist_width/2-side_wall_depth/2, wrist_length/2- side_wall_depth/2, wrist_height - side_wall_depth])
cylinder(side_wall_depth/2, 1+rad_error, 1+rad_error); 

//Bottom Right
translate([wrist_width/2-side_wall_depth/2, -wrist_length/2 + side_wall_depth/2, wrist_height - side_wall_depth])
cylinder(side_wall_depth/2, 1+rad_error, 1+rad_error); 

//Bottom Left
translate([-wrist_width/2+side_wall_depth/2, -wrist_length/2 + side_wall_depth/2, wrist_height - side_wall_depth])
cylinder(side_wall_depth/2, 1+rad_error, 1+rad_error); 

//Top Left
translate([-wrist_width/2+side_wall_depth/2, wrist_length/2 - side_wall_depth/2, wrist_height - side_wall_depth])
cylinder(side_wall_depth/2, 1+rad_error, 1+rad_error); 

*/
translate([-wrist_width/2 -0.5, -wrist_length/2 -0.5, wrist_height - side_wall_depth])
cube([wrist_width +1, wrist_length+1, wrist_height]); 

}

rad_error = 0.1; 
//Top Right
translate([wrist_width/2-side_wall_depth/2, wrist_length/2- side_wall_depth/2, wrist_height - side_wall_depth -side_wall_depth/4])
cylinder(side_wall_depth/2, 1+rad_error, 1+rad_error); 

//Bottom Right
translate([wrist_width/2-side_wall_depth/2, -wrist_length/2 + side_wall_depth/2, wrist_height - side_wall_depth -side_wall_depth/4])
cylinder(side_wall_depth/2, 1+rad_error, 1+rad_error); 

//Bottom Left
translate([-wrist_width/2+side_wall_depth/2, -wrist_length/2 + side_wall_depth/2, wrist_height - side_wall_depth -side_wall_depth/4])
cylinder(side_wall_depth/2, 1+rad_error, 1+rad_error); 

//Top Left
translate([-wrist_width/2+side_wall_depth/2, wrist_length/2 - side_wall_depth/2, wrist_height - side_wall_depth -side_wall_depth/4])
cylinder(side_wall_depth/2, 1+rad_error, 1+rad_error); 


/*
//The removable side?

//Bottom Right when facing side
translate([-side_wall_depth/2 - wrist_width/2 -15 + side_wall_depth - side_wall_depth/4, -wrist_length/2 + side_wall_depth/2, side_wall_depth/2])
rotate([0,90,0])
cylinder(side_wall_depth/2, 1, 1); 

//Top Right
translate([-side_wall_depth/2 - wrist_width/2 -15 + side_wall_depth - side_wall_depth/4, -wrist_length/2 + side_wall_depth/2, wrist_height-side_wall_depth/2])
rotate([0,90,0])
cylinder(side_wall_depth/2, 1, 1); 

//Top Left
translate([-side_wall_depth/2 - wrist_width/2 -15 + side_wall_depth - side_wall_depth/4, wrist_length/2 - side_wall_depth/2, wrist_height-side_wall_depth/2])
rotate([0,90,0])
cylinder(side_wall_depth/2, 1, 1); 

//Bottom Left
translate([-side_wall_depth/2 - wrist_width/2 -15 + side_wall_depth - side_wall_depth/4, wrist_length/2 - side_wall_depth/2, side_wall_depth/2])
rotate([0,90,0])
cylinder(side_wall_depth/2, 1, 1); 

//Make the removable side wall
translate([-side_wall_depth/2 - wrist_width/2 -15 +side_wall_depth/2, -wrist_length/2, 0])
cube([side_wall_depth/2, wrist_length, wrist_height]); 
*/

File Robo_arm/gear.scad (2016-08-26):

//gear.scad
//Laurin Fisher
//June 23, 2016

//Makes a generic gear. The code can be copied then modified for customized use. 

use <robo_arm.scad>; 

pegs = 16; //how many pegs stick out from the circle
gear_height = 5; //The inner circle height
gear_radius = 5; 

peg_width = 15; //Make this bigger than the gear_radius
peg_height = 5; 
peg_depth = 1.5; 


//Module to make a gear with rounded edges using armBase()
module gear(gear_height, gear_radius, pegs, peg_width, peg_depth, peg_height){
    
    //The cylinder size (inner circle)
    cylinder(gear_height, gear_radius, gear_radius); 

    //The pegs, each distributed evenly over the 360 deg
    angle = 360/pegs; 
    for( i = [0:pegs]){
        rotate([0, 0, angle*i])
            armBase(peg_width, peg_height, peg_depth); 
            //comment armBase and uncomment line below for non-rounded gear pegs
            //cube([peg_width, peg_depth, peg_height], 0); 
    }
}

gear(gear_height, gear_radius, pegs, peg_width, peg_depth, peg_height); 

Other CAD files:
layla/SolidWorks/electronics_box/mainboard_pcb.SLDPRT
layla/SolidWorks/electronics_box/bms_assembly.SLDASM
layla/SolidWorks/electronics_box/header_male_1x8.SLDASM
layla/SolidWorks/electronics_box/header_male_1x18.SLDASM
Robo_arm/micro_servo_gear.scad
Robo_arm/STL_files/Top_of_wrist_box.stl
Robo_arm/STL_files/bottom_arm_attach_piece.stl
Robo_arm/STL_files/mid_arm.stl
Robo_arm/STL_files/robo_arm_bottom_1.stl
Robo_arm/STL_files/robo_arm_bottom_2.stl
Robo_arm/STL_files/robo_finger_mark4.stl
Robo_arm/STL_files/robo_hand_gear_box_BOTTOM3.stl
Robo_arm/STL_files/robo_hand_gear_box_TOP4.stl
Robo_arm/STL_files/robo_wrist_cage_side.stl
Robo_arm/STL_files/servo_6_star.stl
Robo_arm/STL_files/wrist_box.stl
Robo_arm/mid_arm.scad
Robo_arm/robo_arm.scad
Robo_arm/robo_finger.scad
Robo_arm/robo_hand_gear_box.scad
Robo_arm/servo_6_star.scad
layla/SolidWorks/11in_barbie_mower.SLDPRT
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

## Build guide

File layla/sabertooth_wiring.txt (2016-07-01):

Sabertooth Wiring:

Looking at the back of the robot this is how the motors are wired for correct direction:
M1A:Left Motor Rear Red Dot
M1B:Left Motor Other
M2A:Right Motor Red Dot
M1B:Right Motor Other

Arduino Pins:
Serial to Saberteeh: Pin 8

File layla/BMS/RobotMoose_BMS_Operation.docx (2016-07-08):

RobotMoose BMS operation

Overview:

The BMS is designed to charge and manage any 3-cell lithium battery. However, the firmware it comes loaded with is specific to Li-Po chemistry voltages, and using it with other chemistries could cause over charging or a fire.

The BMS acts as a shield atop an Arduino Uno platform, and sends battery health and charge data to the main robot controller via I2C protocol.

Connection:

The BMS must be connected correctly before it will allow the robot to power up. The battery positive and negative are connected, as well as the balance leads plugged into the BMS board. The start/estop pin must be connected through a momentary push button to ground. Additionally, “e-stop2” and start/e-stop pins must be connected to each other through a toggle switch. Connected gives normal operation, disconnected or open switch cuts power to the robot.

The charger (12V dc supply) is connected at the CHGR terminal. There is also a battery OUT terminal, which along with the second large GND pin provides power to the rest of the robot.

Finally, SDA, SCL, and GND must be connected to the I2C port of the main control board in order to allow communication between the robot and the BMS.

Operation:

The BMS is connected to the balance plug of the battery, as well as the main power leads of the battery and the power leads of the battery charging supply. During operation, the BMS continually monitors the voltage of each of the 3 cells to ensure that they are within the specified voltage range. Any cell too high or too low will cause the BMS to cut power to the rest of the robot, as well as to itself, in order to keep from discharging the battery into an irreparable state.

To begin operation, the emergency stop toggle must be in the connected position, and the momentary start button must be depressed for about 5 seconds. This pulls the gate of the main power PFET low, providing power to the BMS and the rest of the robot. As the BMS wakes up and performs a battery voltage check, if everything is correct, it will provide power to the gate of an Nfet, which latches the main PFET and allows the momentary button to be released.

If the robot doesn’t stay powered upon releasing the start button, check that the stop switch is in the run position, the balance leads of the battery are connected, and that the battery is not over-charged or over-discharged.

Communication:

For more advanced users, communication with the BMS can be accomplished without RobotMoose. The I2C address of the BMS is 0x02 by default, though this can be easily change by modifying the value of the “ADDRESS” parameter in the BMS firmware. Upon receiving an I2C request from the master, the BMS transmits a three byte packet. The first byte is header with the value 0xCC; this is only used as an error detection and synching mechanism. The next byte contains the charge of the battery in percent, from 0 to 100. The last byte contains the charging and discharging flags, and these are interpreted as shown in Table 1:

Table 1: Bit Field Interpretation for Last Byte of BMS Packet

Bit | Value | Description
0 (LSB) | 0 | Cell #1 is not discharging.
| 1 | Cell #1 is discharging.
1 | 0 | Cell #2 is not discharging.
| 1 | Cell #2 is discharging.
2 | 0 | Cell #3 is not discharging.
| 1 | Cell #3 is discharging.
3 | 0 | Battery is not charging.
| 1 | Battery is charging.
4 | 0 | System is not operating normally. Caused by either the battery being disconnected or by any of the cell voltages being below 3.2V.
| 1 | System is operating normally.
5-7 | 0 | Unused

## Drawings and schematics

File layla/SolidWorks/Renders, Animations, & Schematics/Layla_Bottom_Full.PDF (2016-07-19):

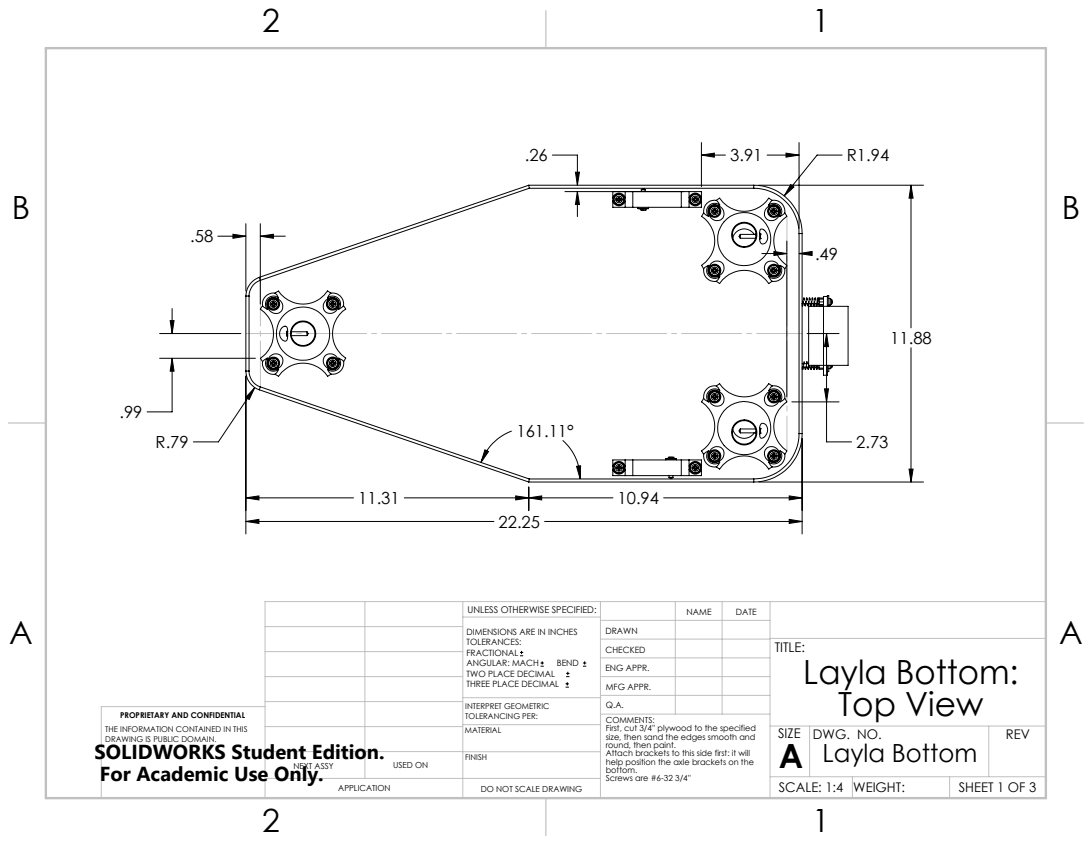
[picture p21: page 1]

UNLESS OTHERWISE SPECIFIED: | | NAME | DATE
DIMENSIONS ARE IN INCHES TOLERANCES: FRACTIONAL ANGULAR: MACH BEND TWO PLACE DECIMAL THREE PLACE DECIMAL | DRAWN

CHECKED | | | TITLE: Layla Bottom: Top View

ENG APPR.
MFG APPR.

INTERPRET GEOMETRIC TOLERANCING PER: | Q.A.
MATERIAL | | SIZE A | DWG. NO. Layla Bottom | REV

PROPRIETARY AND CONFIDENTIAL
THE INFORMATION CONTAINED IN THIS
DRAWING IS PUBLIC DOMAIN.
SOLIDWORKS Student Edition.
For Academic Use Only.

COMMENTS:
First, cut 3/4'' plywood to the specified
size, then sand the edges smooth and
round, then paint.
Attach brackets to this side first: it will
help position the axle brackets on the
bottom.
Screws are #6-32 3/4''

NEXT ASSY | USED ON | FINISH

APPLICATION | DO NOT SCALE DRAWING | | SCALE: 1:4 | WEIGHT: | SHEET 1 OF 3

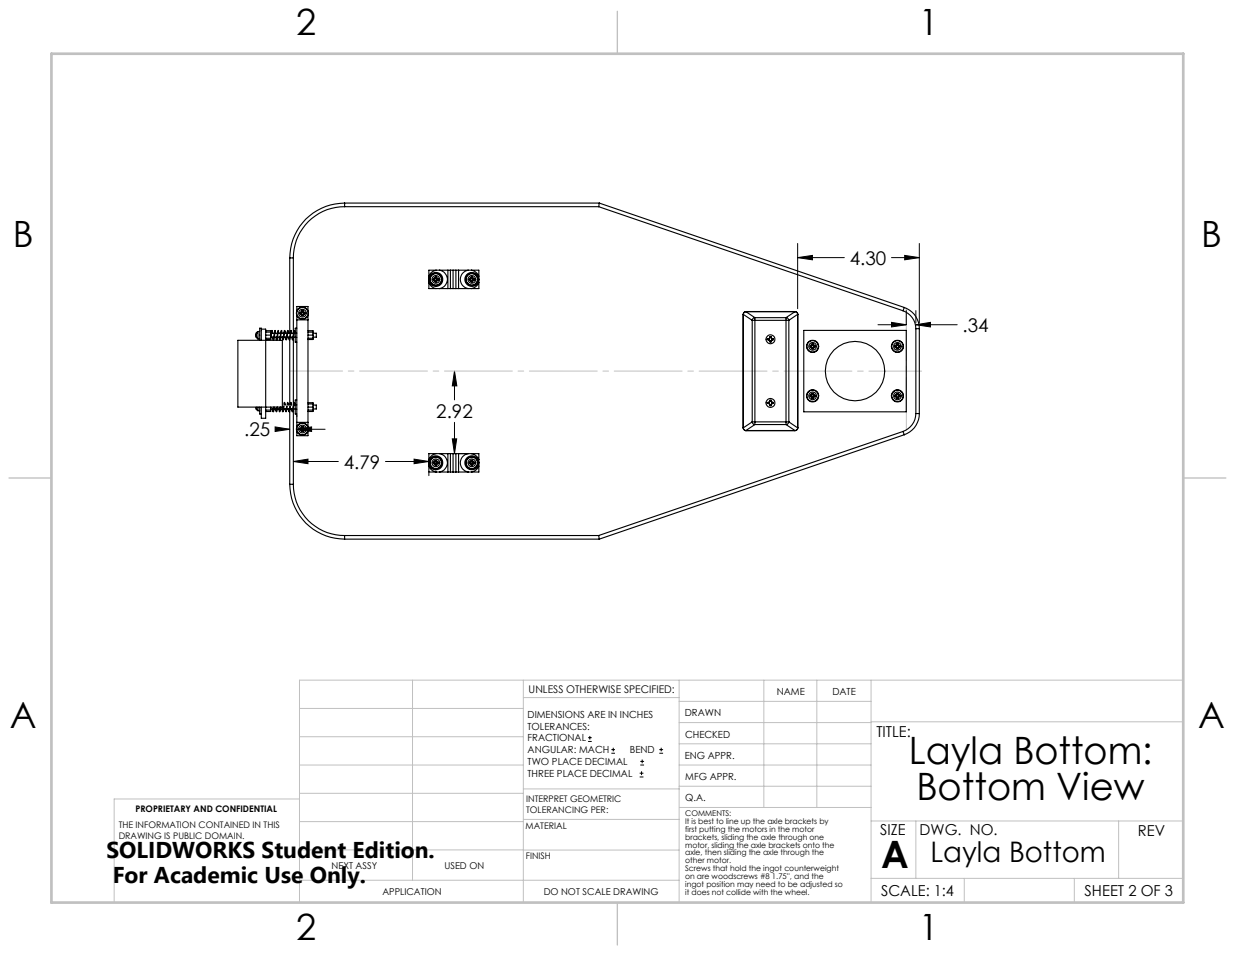
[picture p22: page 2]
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

CHECKED | | | TITLE: Layla Bottom: Bottom View

ENG APPR.
MFG APPR.

INTERPRET GEOMETRIC TOLERANCING PER: | Q.A.
MATERIAL | | SIZE A | DWG. NO. Layla Bottom | REV

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

COMMENTS:
It is best to line up the axle brackets by
first putting the motors in the motor
brackets, sliding the axle through one
motor, sliding the axle brackets onto the
axle, then sliding the axle through the
other motor.
Screws that hold the ingot counterweight
on are woodscrews #8 1.75'', and the
ingot position may need to be adjusted so
it does not collide with the wheel.

NEXT ASSY | USED ON | FINISH

SCALE: 1:4

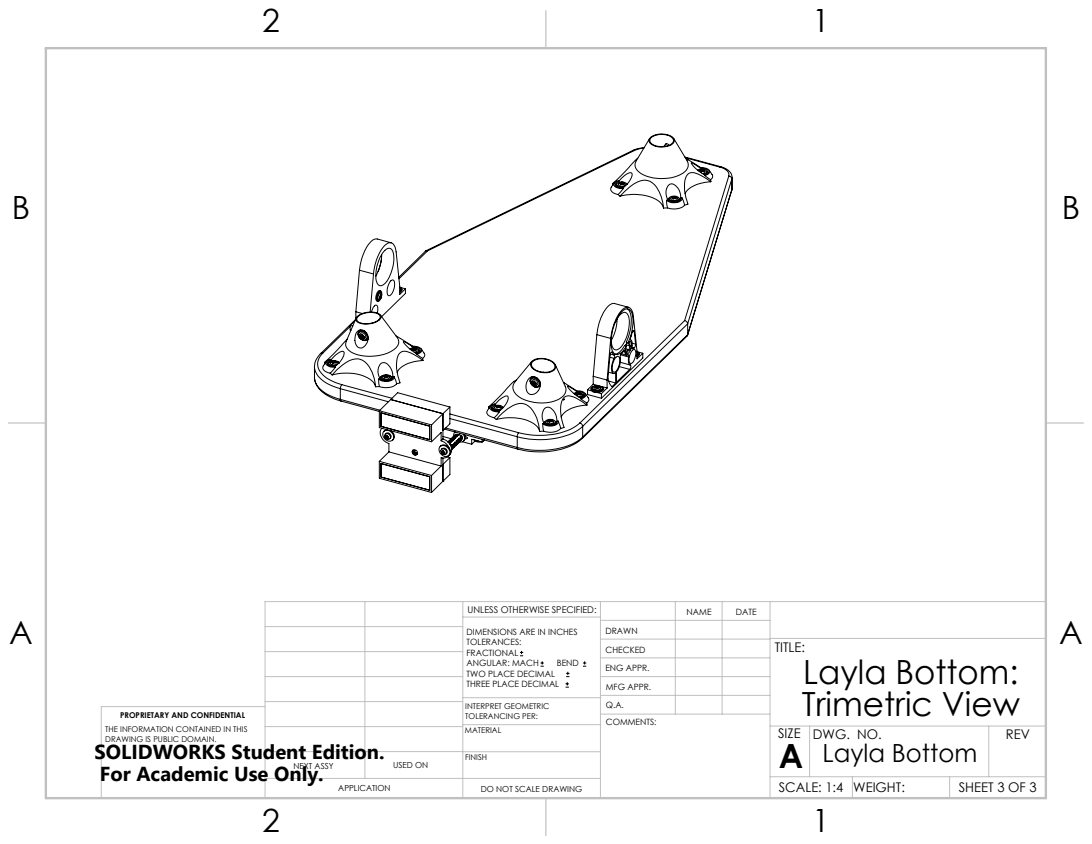
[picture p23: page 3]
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

CHECKED | | | TITLE: Layla Bottom: Trimetric View

ENG APPR.
MFG APPR.

INTERPRET GEOMETRIC TOLERANCING PER: | Q.A.
MATERIAL | | SIZE A | DWG. NO. Layla Bottom | REV

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

NEXT ASSY | USED ON | FINISH

SCALE: 1:4 | WEIGHT:

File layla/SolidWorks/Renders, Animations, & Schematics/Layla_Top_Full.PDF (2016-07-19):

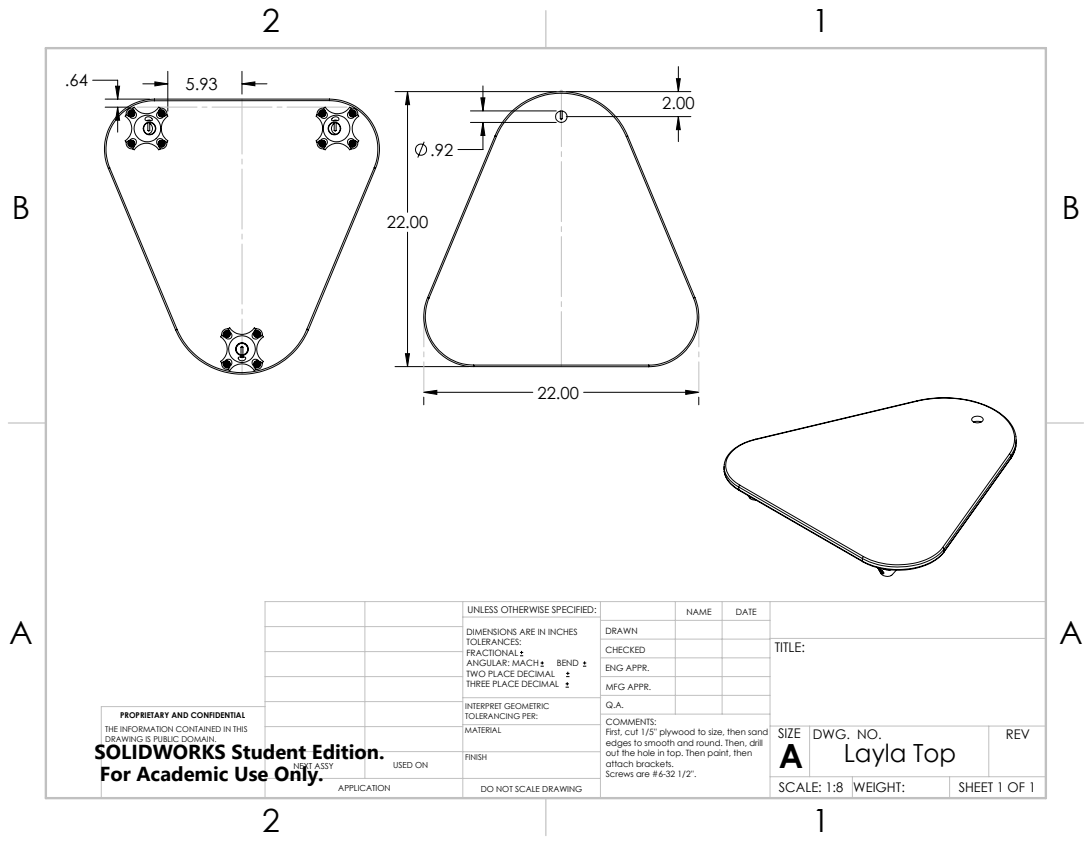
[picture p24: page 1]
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

CHECKED | | | TITLE:

ENG APPR.
MFG APPR.

INTERPRET GEOMETRIC TOLERANCING PER: | Q.A.
MATERIAL | | SIZE A | DWG. NO. Layla Top | REV

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

COMMENTS:
First, cut 1/5'' plywood to size, then sand
edges to smooth and round. Then, drill
out the hole in top. Then paint, then
attach brackets.
Screws are #6-32 1/2''.

NEXT ASSY | USED ON | FINISH

APPLICATION | DO NOT SCALE DRAWING | | SCALE: 1:8 | WEIGHT: | SHEET 1 OF 1

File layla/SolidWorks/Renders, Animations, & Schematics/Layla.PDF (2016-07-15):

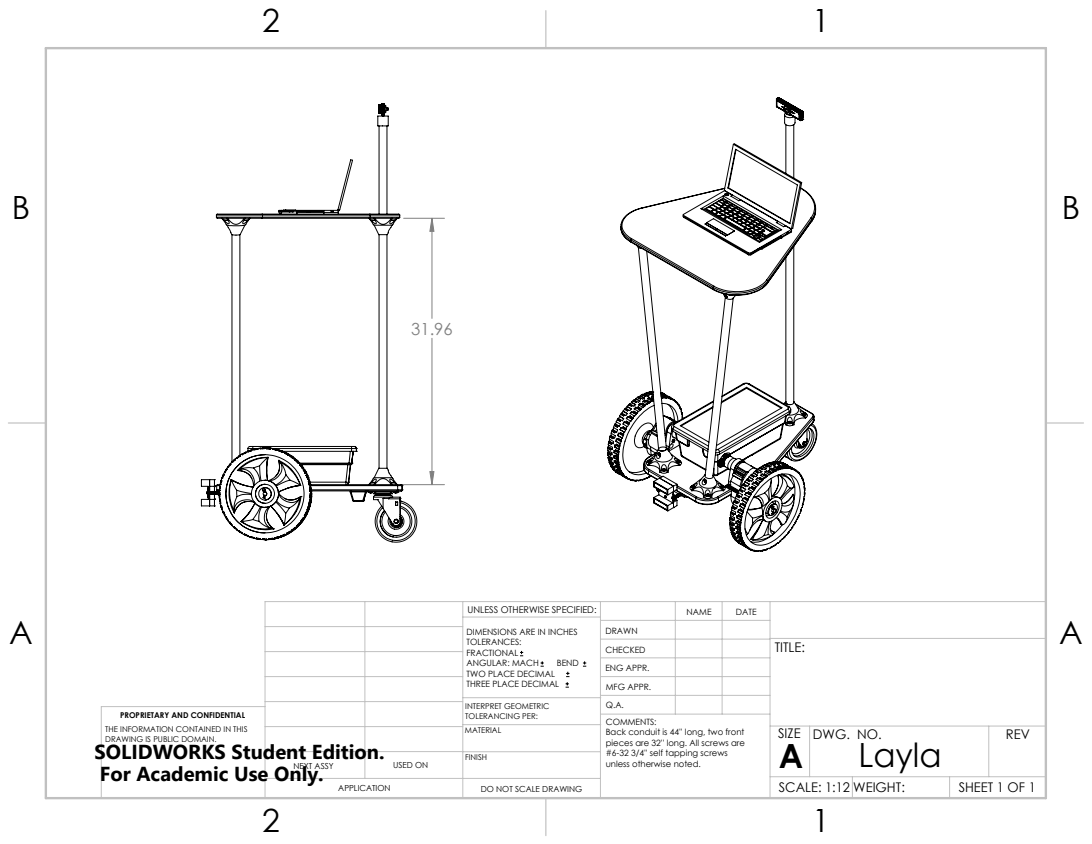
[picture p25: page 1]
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

CHECKED | | | TITLE:

ENG APPR.
MFG APPR.

INTERPRET GEOMETRIC TOLERANCING PER: | Q.A.
MATERIAL | | SIZE A | DWG. NO. Layla | REV

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

COMMENTS:
Back conduit is 44'' long, two front
pieces are 32'' long. All screws are
#6-32 3/4'' self tapping screws
unless otherwise noted.

NEXT ASSY | USED ON | FINISH

APPLICATION | DO NOT SCALE DRAWING | | SCALE: 1:12 WEIGHT: | | SHEET 1 OF 1

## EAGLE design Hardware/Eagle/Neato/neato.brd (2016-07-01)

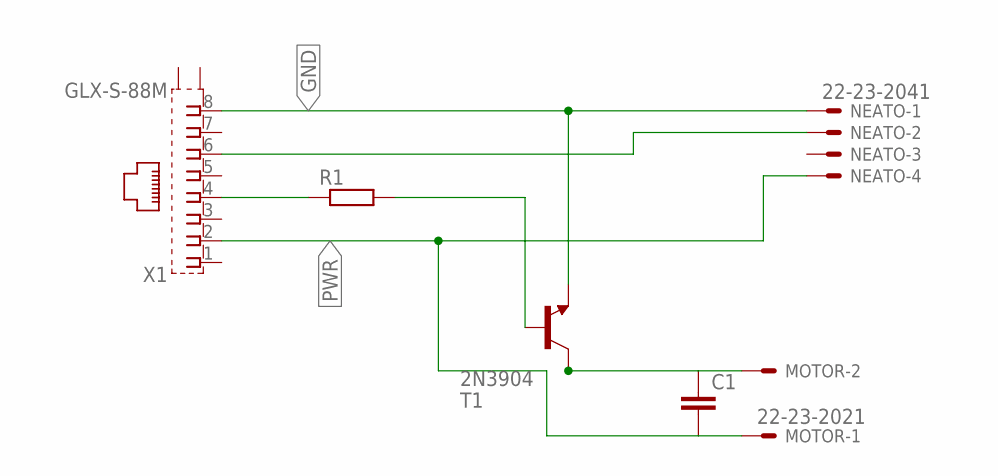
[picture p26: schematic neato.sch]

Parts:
C1: C2,5-3; C2.5-3
MOTOR: 22-23-2021
NEATO: 22-23-2041
R1: R0207/10; 0207/10
T1: 2N3904; TO92
X1: GLX-S-88M

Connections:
GND: NEATO.1, T1.3 (E), X1.8
unnamed: C1.1, MOTOR.2, T1.1 (C)
unnamed: R1.1, X1.4
unnamed: NEATO.2, X1.6
unnamed: R1.2, T1.2 (B)
PWR: C1.2, MOTOR.1, NEATO.4, X1.2

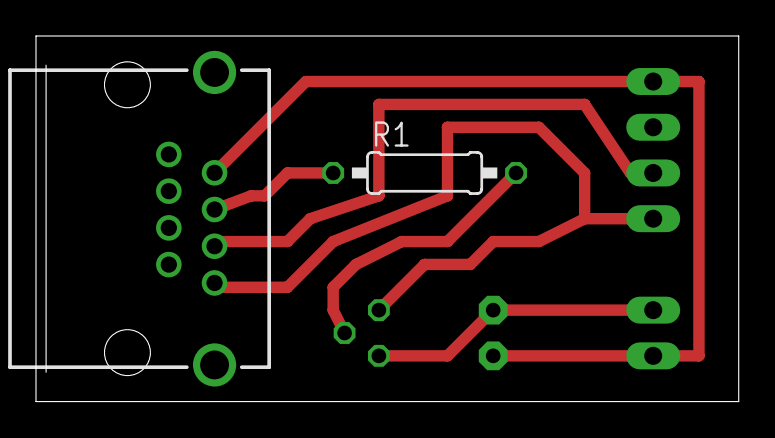
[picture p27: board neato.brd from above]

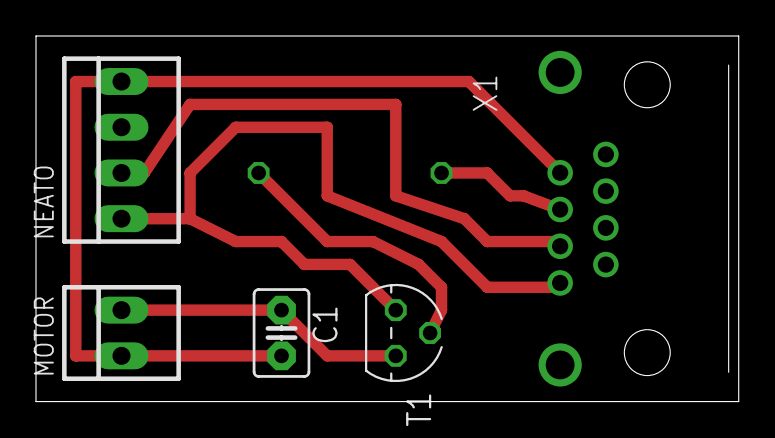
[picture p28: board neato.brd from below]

Board: 1 copper layer, 39.0 x 20.3 mm, 6 parts (5 on the bottom side), 6 nets.

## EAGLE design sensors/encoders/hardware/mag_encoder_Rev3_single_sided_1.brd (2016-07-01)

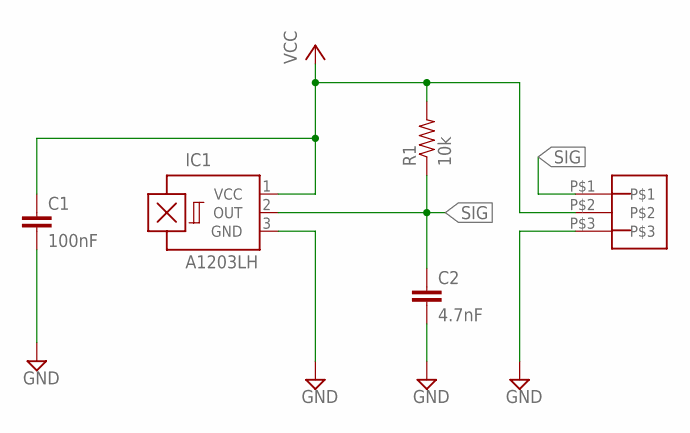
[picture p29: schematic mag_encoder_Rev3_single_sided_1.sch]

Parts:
C1: 100nF; 0603-CAP
C2: 4.7nF; 0603-CAP
IC1: A1203LH; SOT23-W
R1: 10k; 0603
U$1: 3_PIN_JST-XH

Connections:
GND: C1.2, C2.2, IC1.3 (GND), U$1.P$3
SIG: C2.1, IC1.2 (OUT), R1.1, U$1.P$1
VCC: C1.1, IC1.1 (VCC), R1.2, U$1.P$2

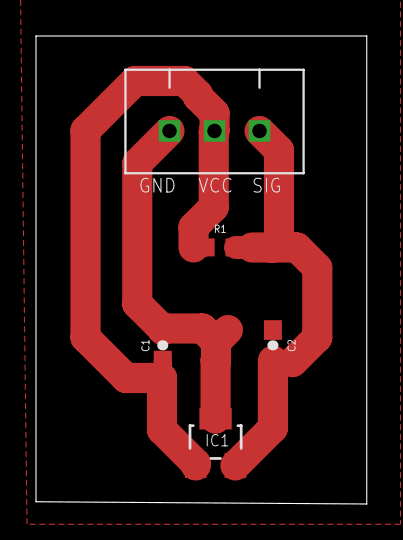
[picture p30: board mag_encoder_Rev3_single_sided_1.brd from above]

Board: 1 copper layer, 18.4 x 26.0 mm, 5 parts (0 on the bottom side), 3 nets.

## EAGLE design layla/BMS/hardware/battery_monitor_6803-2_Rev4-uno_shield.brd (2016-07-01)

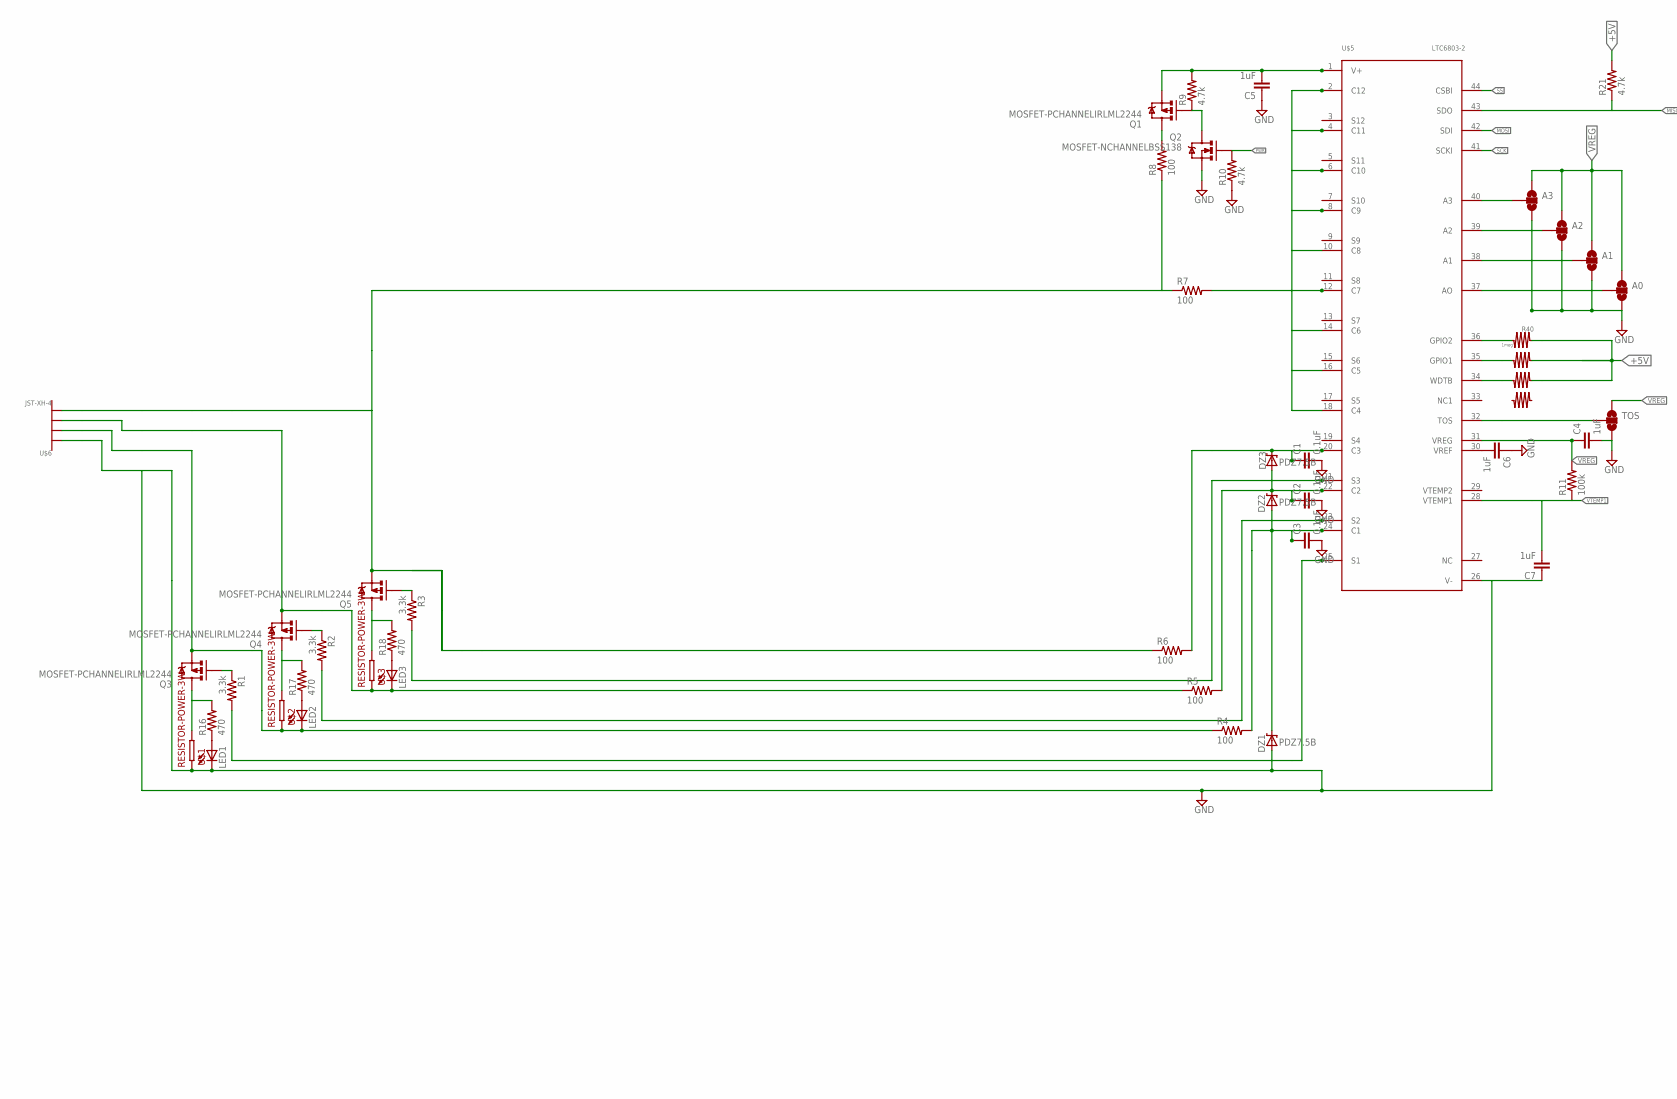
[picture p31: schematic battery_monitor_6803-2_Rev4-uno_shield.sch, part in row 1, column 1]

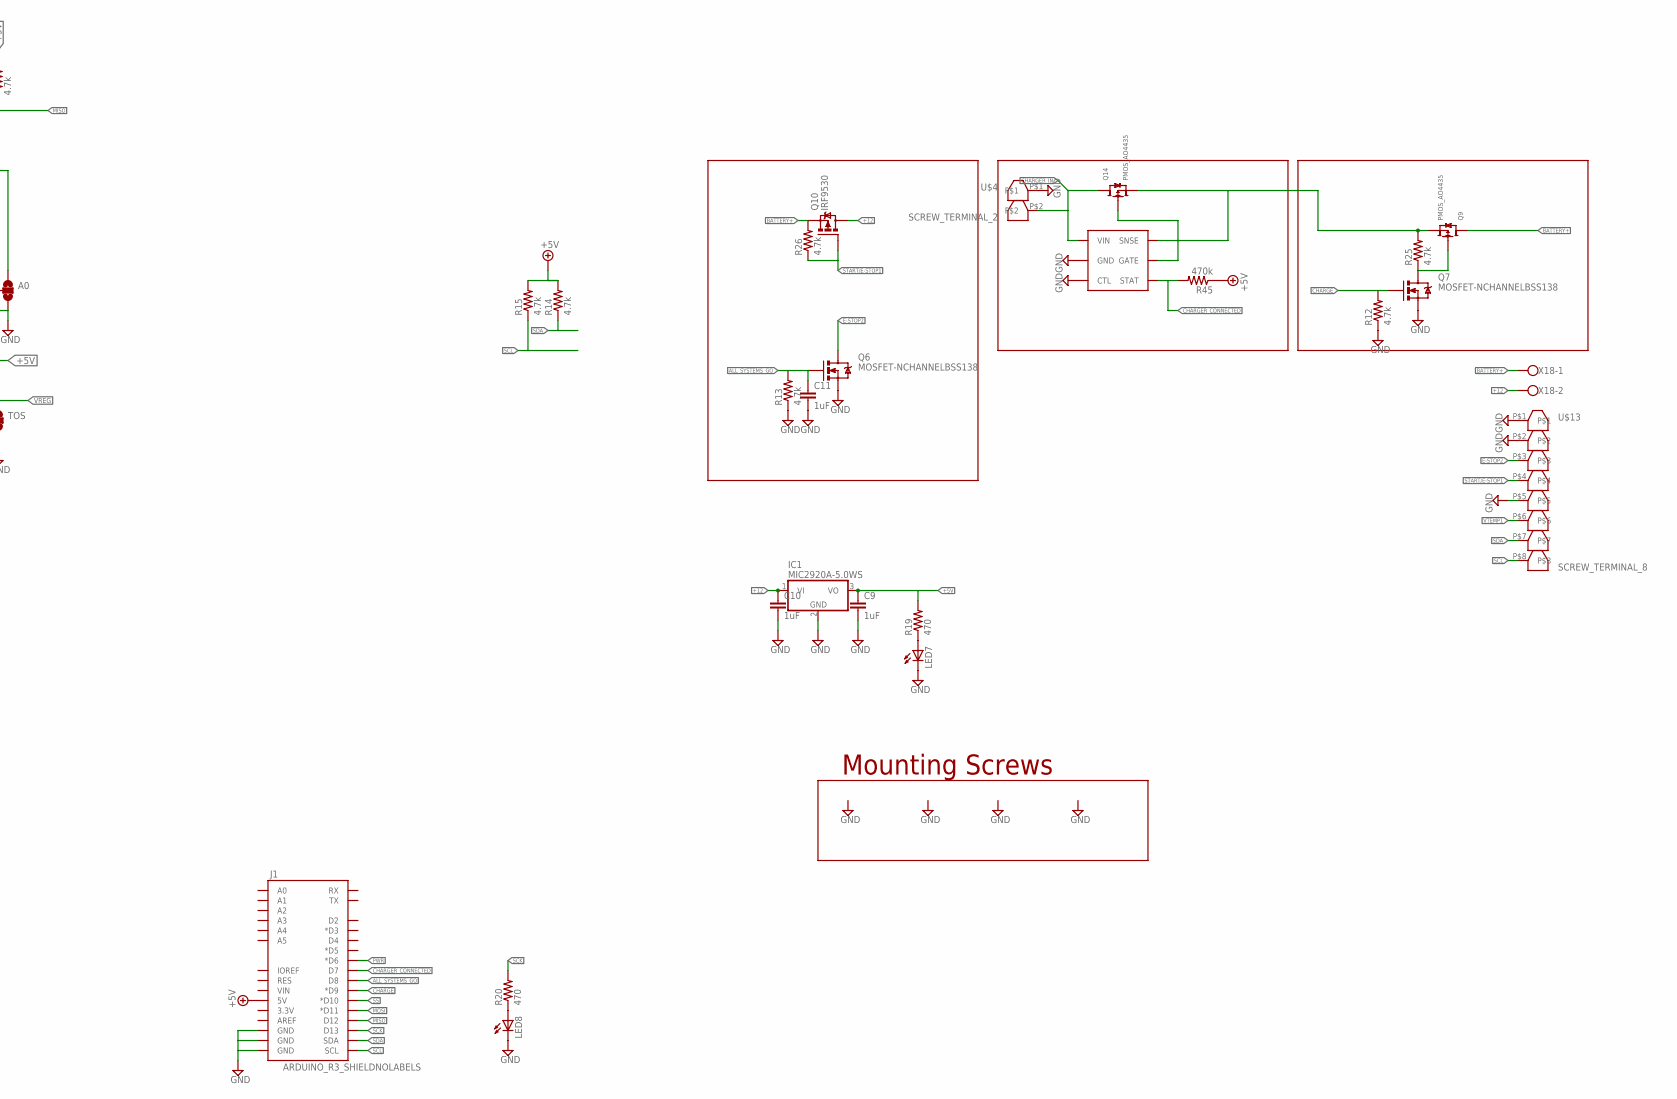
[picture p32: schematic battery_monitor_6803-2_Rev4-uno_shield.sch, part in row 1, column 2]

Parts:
A0, A1, A2, A3: SOLDERJUMPER_2WAYS; SJ_3
C1, C2, C3: 0.1uF; 0603-CAP
C4, C5, C6, C7, C9, C10, C11: 1uF; 0603-CAP
DZ1, DZ2, DZ3: PDZ7.5B; SOD-323
IC1: MIC2920A-5.0WS; SOT223
J1: ARDUINO_R3_SHIELDNOLABELS; UNO_R3_SHIELD_NOLABELS
LED1, LED2, LED3, LED7, LED8: LED0603; LED-0603
Q1, Q3, Q4, Q5: MOSFET-PCHANNELIRLML2244; SOT23-3
Q2, Q6, Q7: MOSFET-NCHANNELBSS138; SOT23
Q9, Q14: PMOS_AO4435; SOIC8
Q10: IRF9530; TO220BV
R1, R2, R3: 3.3k; 0603-RES
R4, R5, R6, R7, R8: 100; 0603-RES
R9, R10, R12, R13, R14, R15, R21, R25, R26: 4.7k; 0603-RES
R11: 100k; 0603-RES
R16, R17, R18, R19, R20: 470; 0603-RES
R40: 1meg; RESISTOR-ARRAY-0603
R45: 470k; 0603-RES
TOS: SOLDERJUMPER_2WAYS; SJ_3
U$1, U$2, U$3: RESISTOR-POWER-3W; RESISTOR-3W
U$4: SCREW_TERMINAL_2
U$5: LTC6803-2; FSOP-44
U$6: JST-XH-4
U$12: LTC4412; SOT-23-6
U$13: SCREW_TERMINAL_8
X18: W237-102

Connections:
+5V: C9.1, IC1.3 (VO), J1.5V, R14.2, R15.2, R19.2, R21.2, R40.P$1, R40.P$3, R40.P$5, R45.1
+12: C10.1, IC1.1 (VI), Q10.D, X18.2
ALL_SYSTEMS_GO: C11.1, J1.D8, Q6.1 (G), R13.2
BATTERY+: Q9.5 (DRAIN), Q9.6 (DRAIN), Q9.7 (DRAIN), Q9.8 (DRAIN), Q10.S, R26.2, X18.1
CHARGE: J1.D9 (*D9), Q7.1 (G), R12.2
CHARGER_CONNECTED: J1.D7, R45.2, U$12.P$4 (STAT)
CHARGER_IN: Q14.5 (DRAIN), Q14.6 (DRAIN), Q14.7 (DRAIN), Q14.8 (DRAIN), U$4.P$2, U$12.P$1 (VIN)
E-STOP2: Q6.3 (D), U$13.P$3
GND: A0.3, A1.3, A2.3, A3.3, C1.2, C2.2, C3.2, C4.2, C5.1, C6.1, C7.1, C9.2, C10.2, C11.2, DZ1.2 (A), IC1.2 (GND), J1.GND@0 (GND), J1.GND@1 (GND), J1.GND@2 (GND), LED1.C, LED7.C, LED8.C, Q2.2 (S), Q6.2 (S), Q7.2 (S), R10.1, R12.1, R13.1, TOS.3, U$1.P$2, U$4.P$1, U$5.26 (V-), U$6.P$4, U$12.P$2 (GND), U$12.P$3 (CTL), U$13.P$1, U$13.P$2, U$13.P$5
MISO: J1.D12, R21.1, U$5.43 (SDO)
MOSI: J1.D11 (*D11), U$5.42 (SDI)
unnamed: Q7.3 (D), Q9.4 (GATE), R25.1
unnamed: LED2.C, Q3.2 (S), R4.1, U$2.P$2, U$6.P$3
unnamed: LED3.C, Q4.2 (S), R5.1, U$3.P$2, U$6.P$2
unnamed: Q5.2 (S), R6.1, R7.1, R8.1, U$6.P$1
unnamed: Q3.3 (D), R16.2, U$1.P$1
unnamed: R2.2, U$5.23 (S2)
unnamed: Q3.1 (G), R1.1
unnamed: R1.2, U$5.25 (S1)
unnamed: R3.2, U$5.21 (S3)
unnamed: Q4.3 (D), R17.2, U$2.P$1
unnamed: Q4.1 (G), R2.1
unnamed: Q5.3 (D), R18.2, U$3.P$1
unnamed: LED1.A, R16.1
unnamed: C1.1, DZ3.1 (C), R6.2, U$5.20 (C3)
unnamed: C3.1, DZ1.1 (C), DZ2.2 (A), R4.2, U$5.24 (C1)
unnamed: C2.1, DZ2.1 (C), DZ3.2 (A), R5.2, U$5.22 (C2)
unnamed: R7.2, U$5.2 (C12), U$5.4 (C11), U$5.6 (C10), U$5.8 (C9), U$5.10 (C8), U$5.12 (C7), U$5.14 (C6), U$5.16 (C5), U$5.18 (C4)
unnamed: Q1.3 (D), R8.2
unnamed: C5.2, Q1.2 (S), R9.2, U$5.1 (V+)
unnamed: Q1.1 (G), Q2.3 (D), R9.1
unnamed: LED7.A, R19.1
unnamed: LED2.A, R17.1
unnamed: LED3.A, R18.1
unnamed: R40.P$2, U$5.36 (GPIO2)
unnamed: R40.P$4, U$5.35 (GPIO1)
unnamed: R40.P$6, U$5.34 (WDTB)
unnamed: A3.2, U$5.40 (A3)
unnamed: Q5.1 (G), R3.1
unnamed: A2.2, U$5.39 (A2)
unnamed: A1.2, U$5.38 (A1)
unnamed: A0.2, U$5.37 (AO)
unnamed: TOS.2, U$5.32 (TOS)
unnamed: C6.2, U$5.30 (VREF)
unnamed: LED8.A, R20.1
unnamed: Q9.1 (SOURCE), Q9.2 (SOURCE), Q9.3 (SOURCE), Q14.1 (SOURCE), Q14.2 (SOURCE), Q14.3 (SOURCE), R25.2, U$12.P$6 (SNSE)
unnamed: Q14.4 (GATE), U$12.P$5 (GATE)
PWR: J1.D6 (*D6), Q2.1 (G), R10.2
SCK: J1.D13, R20.2, U$5.41 (SCKI)
SCL: J1.SCL, R15.1, U$13.P$8
SDA: J1.SDA, R14.1, U$13.P$7
SS: J1.D10 (*D10), U$5.44 (CSBI)
START/E-STOP1: Q10.G, R26.1, U$13.P$4
VREG: A0.1, A1.1, A2.1, A3.1, C4.1, R11.2, TOS.1, U$5.31 (VREG)
VTEMP1: C7.2, R11.1, U$5.28 (VTEMP1), U$13.P$6

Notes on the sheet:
Mounting Screws

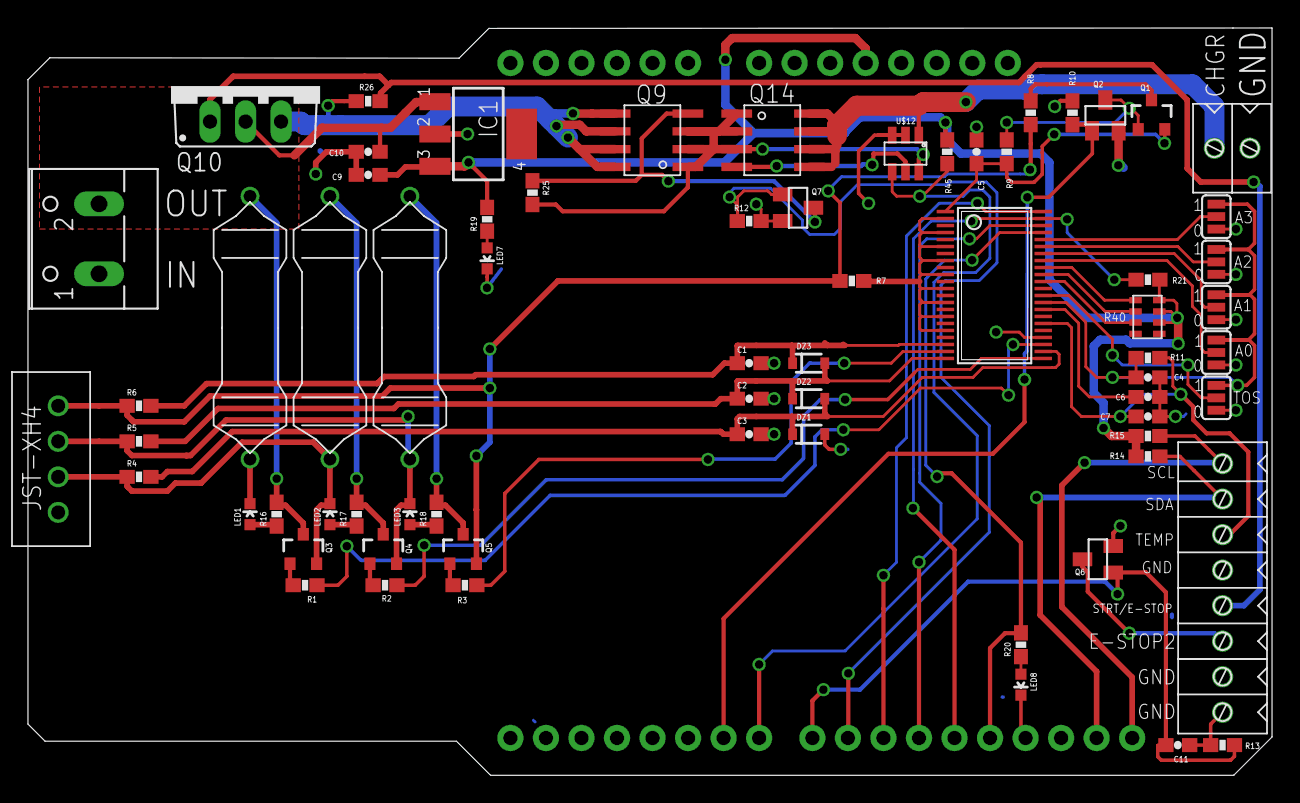
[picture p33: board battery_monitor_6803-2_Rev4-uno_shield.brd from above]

Board: 2 copper layers, 88.9 x 53.4 mm, 69 parts (0 on the bottom side), 55 nets.

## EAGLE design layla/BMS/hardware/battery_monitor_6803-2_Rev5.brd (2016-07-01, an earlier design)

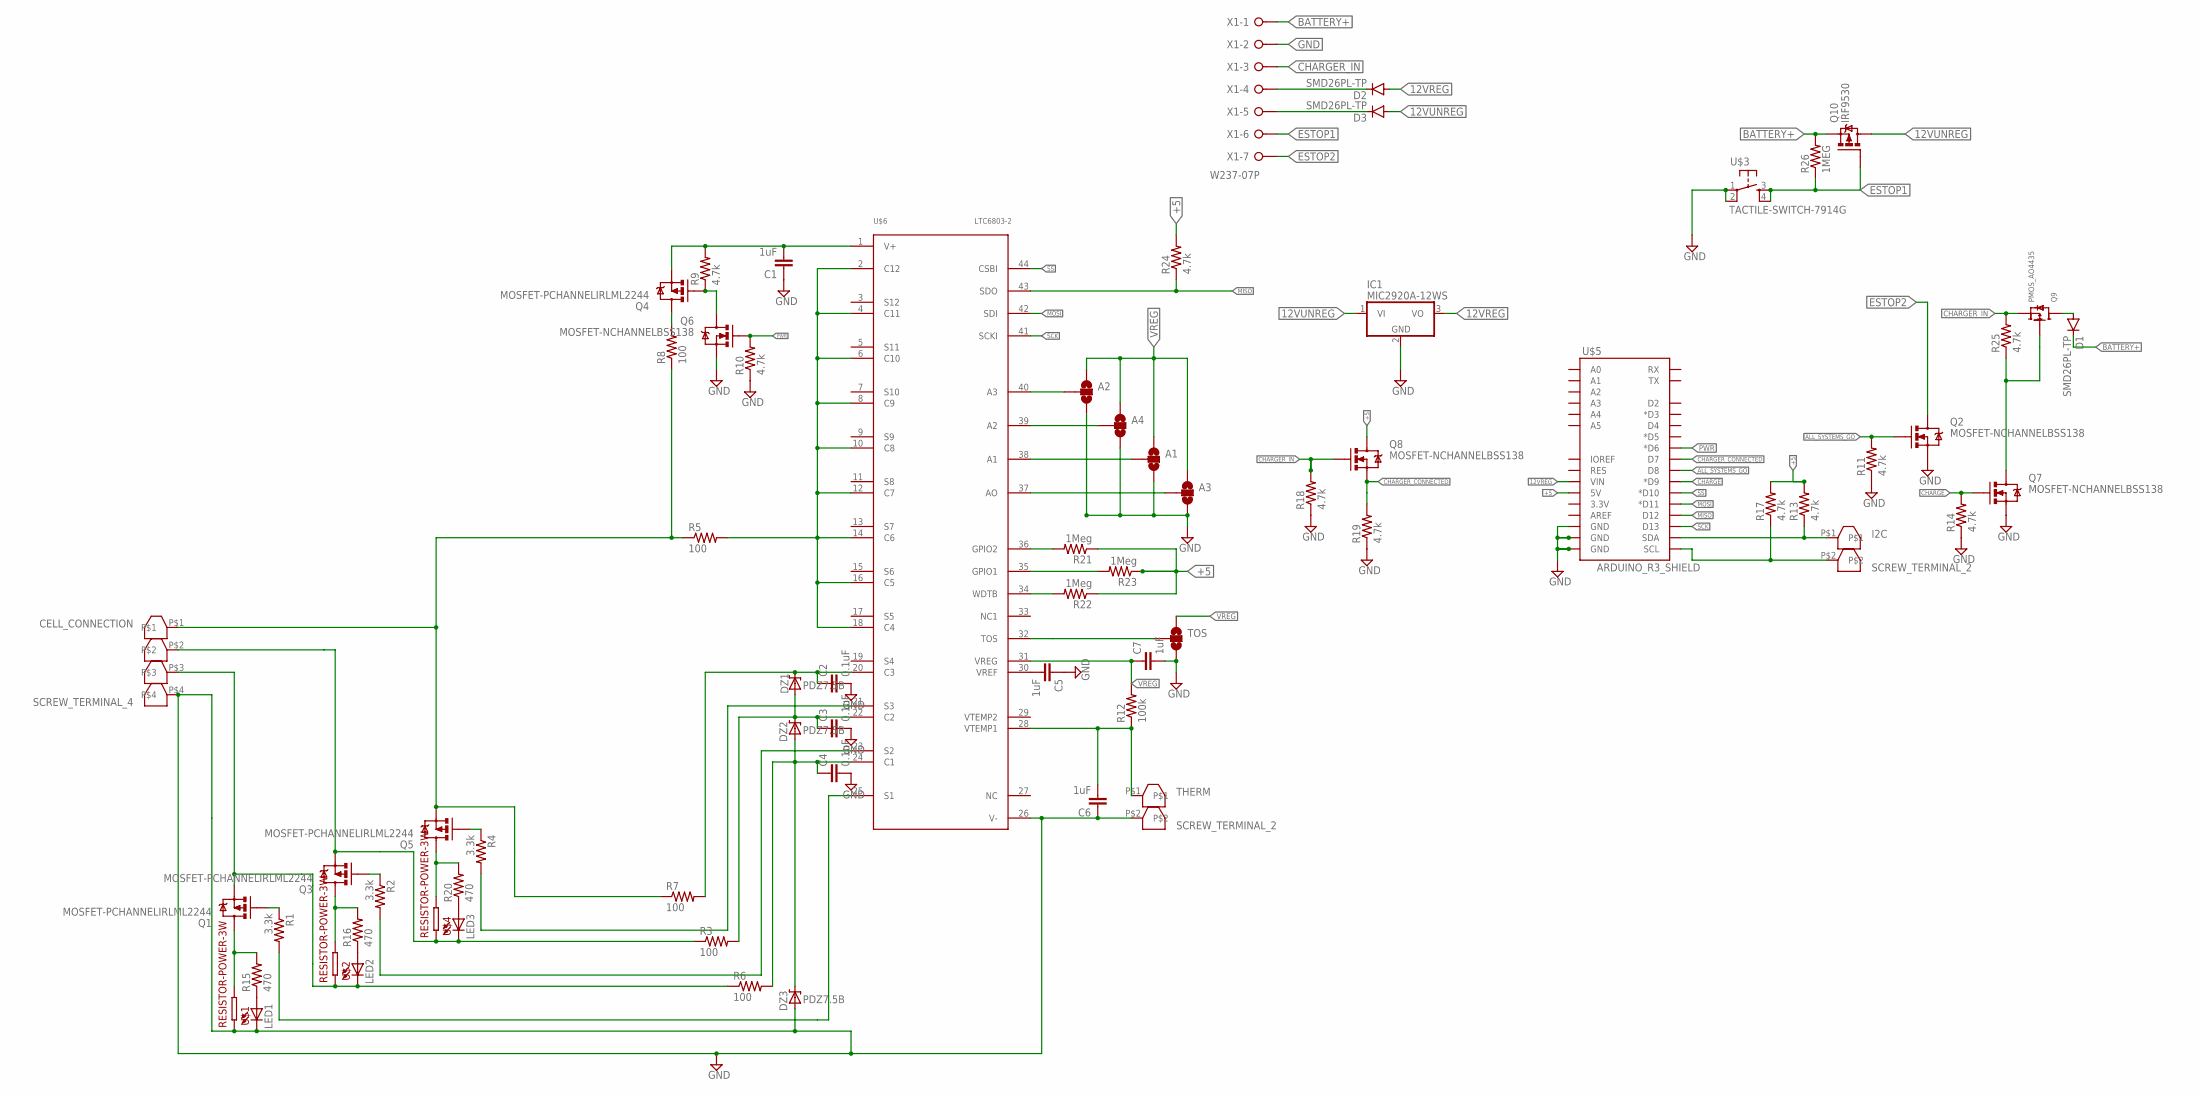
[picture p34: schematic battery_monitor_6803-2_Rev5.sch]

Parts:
A1, A2, A3, A4: SOLDERJUMPER_2WAYS; SJ_3
C1, C5, C6, C7: 1uF; 0603-CAP; MPN C0603X5R0J105M030BC
C2, C3, C4: 0.1uF; 0603-CAP; MPN 0603YG104ZAT2A
CELL_CONNECTION: SCREW_TERMINAL_4; MPN 282834-4
D1, D2, D3: SMD26PL-TP; SOD-123
DZ1, DZ2, DZ3: PDZ7.5B; SOD-323@1; MPN PDZ7.5B,115
I2C: SCREW_TERMINAL_2; MPN 282834-2
IC1: MIC2920A-12WS; SOT223
LED1, LED2, LED3: LED0603; LED-0603; MPN 150060RS75000
Q1, Q3, Q4, Q5: MOSFET-PCHANNELIRLML2244; SOT23-3@1; MPN SI2369DS-T1-GE3
Q2, Q6, Q7, Q8: MOSFET-NCHANNELBSS138; SOT23; MPN IRLML0030TRPBF
Q9: PMOS_AO4435; SOIC8; MPN SI9407BDY-T1-GE3
Q10: IRF9530; TO220BV; MPN NTE2383
R1, R2, R4: 3.3k; 0603-RES; MPN CRCW06033K00FKEA
R3, R5, R6, R7, R8: 100; 0603-RES; MPN ERJ-1GNF1000C
R9, R10, R11, R13, R14, R17, R18, R19, R24, R25: 4.7k; 0603-RES; MPN CRCW06034K70FKEA
R12: 100k; 0603-RES; MPN MC0063W06035100K
R15, R16, R20: 470; 0603-RES; MPN ERJ-P03F4700V
R21, R22, R23: 1Meg; 0603-RES; MPN ERJ-3EKF1004V
R26: 1MEG; 0603-RES; MPN ERJ-3EKF1004V
THERM: SCREW_TERMINAL_2; MPN 282834-2
TOS: SOLDERJUMPER_2WAYS; SJ_3
U$1, U$2, U$4: RESISTOR-POWER-3W; RESISTOR-3W; MPN ERG-3SJ200
U$3: TACTILE-SWITCH-7914G; 7914G; MPN 7914G-1-000E
U$5: ARDUINO_R3_SHIELD; UNO_R3_SHIELD
U$6: LTC6803-2; FSOP-44
X1: W237-07P; W237-7P

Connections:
12VREG: D2.A, IC1.3 (VO), U$5.VIN
12VUNREG: D3.A, IC1.1 (VI), Q10.D
+5: Q8.3 (D), R13.2, R17.2, R21.1, R22.1, R23.1, R24.2, U$5.5V
ALL_SYSTEMS_GO: Q2.1 (G), R11.2, U$5.D8
BATTERY+: D1.C, Q10.S, R26.2, X1.1
CHARGE: Q7.1 (G), R14.2, U$5.D9 (*D9)
CHARGER_CONNECTED: Q8.2 (S), R19.2, U$5.D7
CHARGER_IN: Q8.1 (G), Q9.1 (SOURCE), Q9.2 (SOURCE), Q9.3 (SOURCE), R18.2, R25.2, X1.3
ESTOP1: Q10.G, R26.1, U$3.3, U$3.4, X1.6
ESTOP2: Q2.3 (D), X1.7
GND: A1.3, A2.3, A3.3, A4.3, C1.1, C2.2, C3.2, C4.2, C5.1, C6.1, C7.2, CELL_CONNECTION.P$4, DZ3.2 (A), IC1.2 (GND), LED1.C, Q2.2 (S), Q6.2 (S), Q7.2 (S), R10.1, R11.1, R14.1, R18.1, R19.1, THERM.P$2, TOS.3, U$1.P$2, U$3.1, U$3.2, U$5.GND@0 (GND), U$5.GND@1 (GND), U$5.GND@2 (GND), U$6.26 (V-), X1.2
MISO: R24.1, U$5.D12, U$6.43 (SDO)
MOSI: U$5.D11 (*D11), U$6.42 (SDI)
unnamed: Q7.3 (D), Q9.4 (GATE), R25.1
unnamed: CELL_CONNECTION.P$3, LED2.C, Q1.2 (S), R6.1, U$2.P$2
unnamed: CELL_CONNECTION.P$2, LED3.C, Q3.2 (S), R3.1, U$4.P$2
unnamed: CELL_CONNECTION.P$1, Q5.2 (S), R5.1, R7.1, R8.1
unnamed: Q1.3 (D), R15.2, U$1.P$1
unnamed: R2.2, U$6.23 (S2)
unnamed: Q1.1 (G), R1.1
unnamed: R1.2, U$6.25 (S1)
unnamed: R4.2, U$6.21 (S3)
unnamed: Q3.3 (D), R16.2, U$2.P$1
unnamed: Q3.1 (G), R2.1
unnamed: Q5.3 (D), R20.2, U$4.P$1
unnamed: LED1.A, R15.1
unnamed: C2.1, DZ1.1 (C), R7.2, U$6.20 (C3)
unnamed: C4.1, DZ2.2 (A), DZ3.1 (C), R6.2, U$6.24 (C1)
unnamed: C3.1, DZ1.2 (A), DZ2.1 (C), R3.2, U$6.22 (C2)
unnamed: R5.2, U$6.2 (C12), U$6.4 (C11), U$6.6 (C10), U$6.8 (C9), U$6.10 (C8), U$6.12 (C7), U$6.14 (C6), U$6.16 (C5), U$6.18 (C4)
unnamed: Q4.3 (D), R8.2
unnamed: C1.2, Q4.2 (S), R9.2, U$6.1 (V+)
unnamed: Q4.1 (G), Q6.3 (D), R9.1
unnamed: C6.2, R12.1, THERM.P$1, U$6.28 (VTEMP1)
unnamed: LED2.A, R16.1
unnamed: LED3.A, R20.1
unnamed: R21.2, U$6.36 (GPIO2)
unnamed: R23.2, U$6.35 (GPIO1)
unnamed: D3.C, X1.5
unnamed: R22.2, U$6.34 (WDTB)
unnamed: A2.2, U$6.40 (A3)
unnamed: Q5.1 (G), R4.1
unnamed: A4.2, U$6.39 (A2)
unnamed: A1.2, U$6.38 (A1)
unnamed: A3.2, U$6.37 (AO)
unnamed: TOS.2, U$6.32 (TOS)
unnamed: C5.2, U$6.30 (VREF)
N$$8: D1.A, Q9.5 (DRAIN), Q9.6 (DRAIN), Q9.7 (DRAIN), Q9.8 (DRAIN)
PWR: Q6.1 (G), R10.2, U$5.D6 (*D6)
SCK: U$5.D13, U$6.41 (SCKI)
SCL: I2C.P$2, R17.1, U$5.SCL
SDA: I2C.P$1, R13.1, U$5.SDA
SS: U$5.D10 (*D10), U$6.44 (CSBI)
VREG: A1.1, A2.1, A3.1, A4.1, C7.1, R12.2, TOS.1, U$6.31 (VREG)
WIRE: D2.C, X1.4

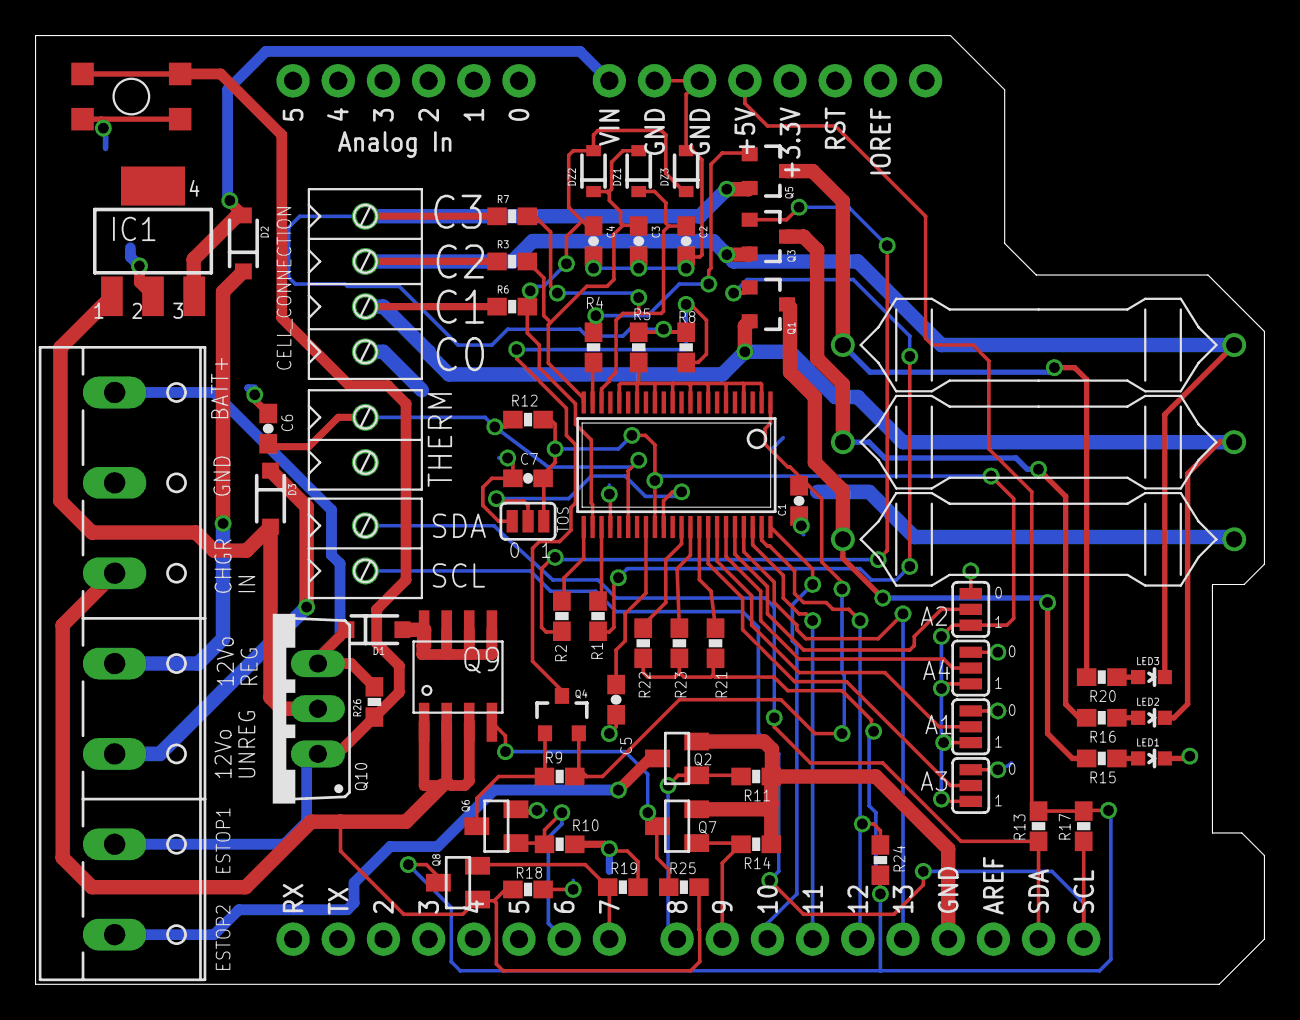
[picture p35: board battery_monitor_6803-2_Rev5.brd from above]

Board: 2 copper layers, 69.1 x 53.3 mm, 68 parts (0 on the bottom side), 55 nets.

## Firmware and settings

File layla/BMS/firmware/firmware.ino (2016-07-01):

// Written By Clayton Auld
// cauld@alaska.edu or clayauld@gmail.com
// Nov 20, 2014

// ITEST Battery Management System for Layla telepresence platform. This BMS system is based on the Linear LTC6803-2 chip.

#include <SPI.h>
#include <Wire.h>
#include <stdlib.h>
#include "percentage.h"

// LTC6803 parameters

#define WRCFG        0x01 // Write configuration register group
#define RDCFG        0x02 // Read configuration register group
#define RDCV         0x04 // Command to read all cell voltages
#define RDCVA        0x06 // Command to read cell voltages 1-4
#define RDCVB        0x08 // Read cell voltages 5-8
#define RDCVC        0x0A // Read cell voltage 9-12
#define RDFLG        0x0C // Read flag register group
#define RDTMP        0x0E // Read temperature register group
#define STCVAD       0x10 // Start cell voltage ADC conversions and poll status
#define STCST1       0x1E // ADC conversion self test 1
#define STCST2       0x1F // ADC conversion self test 2
#define STOWAD       0x20 // Start open-wire ADC conversions and poll status
#define STTMPAD      0x30 // Start temperature ADC conversions and poll status
#define PLADC        0x40 // Poll ADC Converter status
#define PLINT        0x50 // Poll interrupt status
#define DAGN         0x52 // Start diagnose and poll status
#define RDDGNR       0x54 // Read Diagnostic register
#define STCVDC       0x60 // Start cell voltage ADC conversions and poll status, with discharge permitted
#define STOWDC       0x70 // Start open-wire ADC conversions and poll status, with discharge permitted
#define CLEAR        0x1D // Clear the cell voltage registers and temperature registers

// Charge function parameters

#define ABS_max           4.2  // Max Cell voltage: DO NOT CHARGE HIGHER
#define max_working       4.15  // Discharge cells higher than this value
#define low_cell_working  3.500  // Warning Voltage
#define ABS_min           3.200  //E-Stop or risk damage

// Configuration Registers for measure mode

#define CFGR0       0xE1
byte CFGR1=0x00;              
#define CFGR2       0x00
#define CFGR3       0xFF
#define CFGR4       0x00
#define CFGR5       0x00

// Arduino Pins

#define SS_PIN        10   // Designate Chip select pin ***Change this to pin 53 when uploading to Mega***
#define CHARGE_INPUT  7    // Will be pulled high when AC power is available
#define CHARGE_RELAY  9    // Set to high to turn on charging relay
#define CHARGE_LED_PIN 5
#define POWER         6    // Power pin for BMS shield
#define ADDRESS       0x02 // Designate Chip address: 10000000
#define OK_PIN        8    // OK signal for system power

//---------------------------------------------------------------------------------------------------------------------
// Calculation Variables
//byte conf[6];                // Only needed when GetConfig() function is in use.
unsigned int RawData[6];       // Raw data from voltage registers
float cellVoltage[3];          // Calculated voltages for each cell
float AvgCellVolts;
float cellVoltTotal;
byte chargeflag;               // 1 if charging, 0 otherwise
byte ok_flag;                  // 1 if OK pin set to high, 0 otherwise

// PEC Variables
static byte crc8_table[256];   // 8-bit table for PEC calc
static int made_table = 0;     // table made flag
byte packet[18]={0};           // used for PEC calc
// NOT NEEDED PEC Variables
//byte PECbyte;                // PEC of a byte
//byte PECpacket;              // PEC of packet
//byte PECpacketREAD;          // value that PECpacket should be as read from 6803

// Debug Variables
bool debug = false;
uint32_t time_debug = 0;
//---------------------------------------------------------------------------------------------------------------------

//int x=0;

void setup()
{
  pinMode(OK_PIN, OUTPUT);
  pinMode(POWER, OUTPUT);
  digitalWrite(OK_PIN, HIGH); // Set OK signal to HIGH
  digitalWrite(POWER, HIGH); // Allow Arduino to stay powered
  pinMode(SS_PIN, OUTPUT);
  pinMode(CHARGE_INPUT, INPUT);
  pinMode(CHARGE_RELAY, OUTPUT);
  pinMode(CHARGE_LED_PIN, OUTPUT);
  digitalWrite(SS_PIN, HIGH); // Chip Deselect

  // SPI Configuration: MSB First, CPOL = 1, CPHA = 1, DIV16 = 1Mhz
  SPI.setBitOrder(MSBFIRST);
  SPI.setDataMode(SPI_MODE3);
  SPI.setClockDivider(SPI_CLOCK_DIV16);

  SPI.begin();          // Start SPI
  Serial.begin(115200);   // Open serial port
  Serial.println("Setup Done");
//---------------------------------------------------------------------------------------------------------------------

// I2C configs
 Wire.begin(ADDRESS);          // join i2c bus
 Wire.onRequest(requestEvent); // register event

//---------------------------------------------------------------------------------------------------------------------

}

void SetConfig()  // Send configuration registers to put LTC6803 into "Measure mode."
{
  //Serial.println("Writing Configuration Registers");
  digitalWrite(SS_PIN, LOW); // Chip Select
  SPI.transfer(WRCFG);
  SPI.transfer(0xC7);
  SPI.transfer(CFGR0);
  SPI.transfer(CFGR1);
  SPI.transfer(CFGR2);
  SPI.transfer(CFGR3);
  SPI.transfer(CFGR4);
  SPI.transfer(CFGR5);
  packet[0]=CFGR0;
  packet[1]=CFGR1;
  packet[2]=CFGR2;
  packet[3]=CFGR3;
  packet[4]=CFGR4;
  packet[5]=CFGR5;
  SPI.transfer(calcPECpacket(6));
  digitalWrite(SS_PIN, HIGH); // Chip Deselect
}

// This code is only needed to verify that the configuration registers are getting written to correctly
void GetConfig()
{
  digitalWrite(SS_PIN, LOW);
  SPI.transfer(RDCFG);
  SPI.transfer(0xCE);
  int conf[6];
  for(int i=0; i<6; i++)
  {
    conf[i] = SPI.transfer(0x00);
    Serial.println(conf[i], HEX);
  }
  digitalWrite(SS_PIN, HIGH);
}


unsigned int getCellVolts()
{
  digitalWrite(SS_PIN, LOW); // Chip Select
  SPI.transfer(RDCV); // Send command to read cells 1-4
  SPI.transfer(0xDC); // Send PEC byte for command
  //Serial.println("Reading Cell Voltage Registers");

  for(int i=0; i<6; i++)
  {
    RawData[i] = SPI.transfer(0x00);   // send command to read voltage registers
    //Serial.println(RawData[i], HEX);
  }
  byte PECresponse;
  PECresponse=SPI.transfer(0x00);
  digitalWrite(SS_PIN, HIGH); // Chip Deselect
  return RawData[6];
}

void ADCconvert()  // Send command to run ADC conversion
{
  //Serial.println("ADC conversion started");
  digitalWrite(SS_PIN, LOW); // Chip Select
  SPI.transfer(STCVDC); // Send command to start ADC conversion
  SPI.transfer(0xE7); // Send PEC byte for command
  digitalWrite(SS_PIN, HIGH); // Chip Deselect
}

unsigned int BitShiftCombine(unsigned char x_high, unsigned char x_low)  // Combine 2 registers into 16-bit number
{
  unsigned int combined;
  unsigned int Cell0;
  combined = x_high;                        //send x_high to rightmost 8 bits
  combined = combined << 8;                 //shift x_high over to leftmost 8 bits
  combined = combined | x_low;              //logical OR keeps x_high intact in combined and fills in rightmost 8 bits
  return combined;
}

int CellConvert(unsigned int combined1, unsigned int combined2, unsigned int combined3)  // Convert 16-bit number to correct 12-bit number for voltage calculation
{
  int Cell[3];
  Cell[0] = combined1 & 4095;
  Cell[1] = combined2 >> 4;
  Cell[2] = combined3 & 4095;
  for(int i=0; i<3; i++)
  {
    cellVoltage[i] = 1.5/1000*(Cell[i] - 512);
  }
  if ((cellVoltage[0] + cellVoltage[1] + cellVoltage[2]) >= 16)
  {
    cellVoltage[0] = 0;
    cellVoltage[1] = 0;
    cellVoltage[2] = 0;
  }
  return cellVoltage[3];
}

float AvgerageCell()
{
  AvgCellVolts=(cellVoltage[0]+cellVoltage[1]+cellVoltage[2])/3;
  return AvgCellVolts;
}

float totalCell()
{
  cellVoltTotal = cellVoltage[0] + cellVoltage[1] + cellVoltage[2];
  return cellVoltTotal;
}

void setCFGR1( float cellVoltage[], byte & CFGR1 )
{
  CFGR1 = 0; //Clears out GFGR1
  if (cellVoltage[0] >= max_working)
  {
    CFGR1 += 0x01; //Sets DCC1 = 1
  }
  if (cellVoltage[1] >= max_working)
  {
    CFGR1 += 0x02; //Sets DCC2 = 1
  }
  if (cellVoltage[2] >= max_working)
  {
    CFGR1 += 0x04; //Sets DCC3 = 1
  }
}

void Charge()    // Function to turn on charging and cell balancing
{
  // Artificially set to test if statements:
  //cellVoltage[0] = 3.3;
  //cellVoltage[1] = 3.1;
  //cellVoltage[2]=  3.2;
  //digitalWrite(CHARGE_INPUT, HIGH);


  //Sets CFGR1 to manage cell discharging
  setCFGR1(cellVoltage, CFGR1);
  SetConfig();
  if (digitalRead(CHARGE_INPUT) == HIGH)
  {
    Serial.println("Charger Connected");
    digitalWrite(CHARGE_LED_PIN, HIGH);
    //If a single cell's voltage is greater than the absolute max, turns off charging
    if ((cellVoltage[0] >= ABS_max) || (cellVoltage[1] >= ABS_max) || (cellVoltage[2] >= ABS_max))
    {
      digitalWrite(CHARGE_RELAY, LOW);
      chargeflag=0;
    }
    //If not charging is OK
    else
    {
      chargeflag=1;
      digitalWrite(CHARGE_RELAY, HIGH);
    }
  }
  else if (digitalRead(CHARGE_INPUT) == LOW)
  {
    Serial.println("Charger Disconnected");
    digitalWrite(CHARGE_LED_PIN, LOW);
    digitalWrite(CHARGE_RELAY, LOW);
    chargeflag=0;
  }
}

void BatteryCritical()
{
  // Artificially set to test if statements:
  //cellVoltage[0] = 4.16;
  //cellVoltage[1] = 4.16;
  //cellVoltage[2]=  4.16;
  if ((cellVoltage[0] + cellVoltage[1] + cellVoltage[2]) == 0)
  {
    digitalWrite(OK_PIN, LOW);
    ok_flag = 0;
    Serial.println("Battery is DISCONNECTED!\nSYSTEM OK pin set to LOW.");
  }
  else if ((cellVoltage[0] <= ABS_min) || (cellVoltage[1] <= ABS_min) || (cellVoltage[2] <= ABS_min))
  //else if (Percentage(cellVoltTotal) <= 0)
  {
    if (digitalRead(CHARGE_INPUT) == LOW)
    {
      digitalWrite(OK_PIN, LOW); //Set the OK signal low
      ok_flag = 0;
      digitalWrite(POWER, LOW); //Set the BMS power to off
      Serial.println("Battery is AT OR BELOW MINIMUM VOLTAGE!\nSYSTEM OK pin set to LOW.");
    }
    else if (digitalRead(CHARGE_INPUT == HIGH))
    {
      digitalWrite(OK_PIN, LOW);
      ok_flag = 0;
      Serial.println("Battery is AT OR BELOW MINIMUM VOLTAGE!\nSYSTEM OK pin set to LOW.");
    }
  }
  else
  {
    digitalWrite(OK_PIN, HIGH);
    ok_flag = 1;
    Serial.println("Battery level is above minimum.\nSYSTEM OK pin set to HIGH.");
  }
}

/*
int findHighCell(float cellVoltage[])
{
int cell[4];
int highCell = cell[0];
for(int i = 1; i <= totalCells; i++)
{
if(cellVoltage[i] > cellVoltage[i-1])
highCell = cell[i];
}
return highCell;
}
*/

//---------------------------------------------------------------------------------------------------------------------
// Following PEC code by Dale (KiloOne) on Endless Sphere
// http://endless-sphere.com/forums/viewtopic.php?f=14&t=40962

void init_crc8() // Generate PEC lookup table
{
  int z,j;
  byte cr;
  if (!made_table) {
    for (z = 0; z < 256; z ++) {
      cr = z;
      for (j = 0; j < 8; j ++) {
        cr = (cr << 1) ^ ((cr & 0x80) ? 0x07 : 0);
      }
      crc8_table[z] = cr & 0xFF;
    }
    made_table = 1;
  }
}

byte calcPECbyte(byte m) // Calculate PEC from single byte
{
  byte PECbyte = 0x41;  // initialize PECbyte
  if (!made_table) {  // Check and make sure lookup table is generated
    init_crc8();  // Generate Table
  }
  PECbyte = crc8_table[(PECbyte) ^ m];
  return PECbyte;
}

byte calcPECpacket(byte np) // Calculate PEC for an array of bytes. np is number of bytes currently in packet[]
{
  //int z;
  byte PECpacket = 0x41;  // initialize PECpacket
  if (!made_table) {  // Check and make sure lookup table is generated
    init_crc8();  // Generate Table
  }
  for (int z = 0; z < np; z ++) {
    PECpacket = crc8_table[(PECpacket) ^ packet[z]];
  }
  return PECpacket;
}

//---------------------------------------------------------------------------------------------------------------------
// I2C communication code

// Upon I2C request, sends a packet containing battery percentage and charge/discharge information.
void requestEvent()
{
  byte header = 0xCC;
  float charge_percent = Percentage(cellVoltTotal);
  byte charge_byte = getChargeByte();
  
  byte data[ 3*sizeof(byte) ] = { header, (byte)charge_percent, charge_byte };
  // Packet begins with a byte header of 0xCC
  // Next sizeof(float) bytes are a float containing the battery percentage
  // The last byte contains charging and discharging info. Check getChargeByte() description for format.
  
  Wire.write( data, 3*sizeof(byte) );
  /*Wire.write( header );
  Wire.write( (byte *)&charge_percent, sizeof(float) );
  Wire.write( charge_byte );*/
}

// Returns a byte with charging and discharging information
// Bit 0 is 1 if cell #1 is discharging, 0 otherwise
// Bit 1 is 1 if cell #2 is discharging, 0 otherwise
// Bit 2 is 1 if cell #3 is discharging, 0 otherwise
// Bit 3 is 1 if the battery is charging, 0 otherwise
// Bit 4 is 1 if BMS is OK, 0 otherwise.
// Bits 5-7 are unused
byte getChargeByte()
{
  return 0x00 | (ok_flag << 4) | ((chargeflag << 3) | CFGR1);
}

//---------------------------------------------------------------------------------------------------------------------
//---------------------------------------------------------------------------------------------------------------------
void loop()
{
  digitalWrite(POWER, HIGH);
  //GetConfig();                    // Only needed for debugging purposes.
  SetConfig();
  //GetConfig();                    // Only needed for debugging purposes.
  ADCconvert();
  getCellVolts();
  cellVoltage[3]=CellConvert(BitShiftCombine(RawData[1], RawData[0]), BitShiftCombine(RawData[2], RawData[1]), BitShiftCombine(RawData[4], RawData[3]));

  if(Serial.available() > 0) {
    char command = Serial.read();
    if(command == 'D') debug = true;
    time_debug = millis();
  }

  if(debug) {
    if(millis() - time_debug < 1000) {
      cellVoltage[0] = 4.16;
    }
    else if(millis() - time_debug < 2000) {
      cellVoltage[1] = 4.16;
    }
    else if(millis() - time_debug < 3000) {
      cellVoltage[2]=  4.16;
    }
    else if (millis() - time_debug < 4000) {
      cellVoltage[0] = 4.16;
      cellVoltage[1] = 4.16;
      cellVoltage[2]=  4.16;  
    }
    else {
      debug = false;
    }
  }
  
  BatteryCritical();
  AvgerageCell();
  totalCell();
  Charge();

  
  
  Serial.print("Charge flag: ");
  Serial.println(chargeflag,3);

  for(int i=0; i<3; i++)
  {
    Serial.print("Cell ");
    Serial.print(i);
    Serial.print(": ");
    Serial.print(cellVoltage[i], 3);
    Serial.println(" V");
  }
  Serial.print("Average Cell Voltage: ");
  Serial.print(AvgCellVolts,3);
  Serial.println(" V");

  Serial.print("Total Cell Voltages: ");
  Serial.print(cellVoltTotal,3);
  Serial.println(" V");

  Serial.print("Battery Percentage: ");
  Serial.print(Percentage(cellVoltTotal));
  Serial.println(" %");

  Serial.println("-------------------------------------");
  //yedelay(1200);
}
//---------------------------------------------------------------------------------------------------------------------
//---------------------------------------------------------------------------------------------------------------------

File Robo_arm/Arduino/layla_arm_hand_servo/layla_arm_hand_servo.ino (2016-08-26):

#include <Servo.h>  // servo library

Servo left_hand_servo;  // servo control object
Servo right_finger_servo; 

void setup()
{
  // Attach tells the Arduino to begin sending control signals
  // to the servo. Servos require a continuous stream of control
  // signals, even if you're not currently moving them.
  // While the servo is being controlled, it will hold its 
  // current position with some force. If you ever want to
  // release the servo (allowing it to be turned by hand),
  // you can call servo1.detach().

  left_hand_servo.attach(9);
  right_finger_servo.attach(10); 
}


void loop()
{
  int position;
  
  // To control a servo, you give it the angle you'd like it
  // to turn to. Servos cannot turn a full 360 degrees, but you
  // can tell it to move anywhere between 0 and 180 degrees.

  left_hand_servo.write(90); 
 // right_finger_servo.write(90);

  delay(1000); 

  left_hand_servo.write(108); 
 // right_finger_servo.write(108); 

  delay(1000); 

  
  // Change position at a slower speed:

  // To slow down the servo's motion, we'll use a for() loop
  // to give it a bunch of intermediate positions, with 20ms
  // delays between them. You can change the step size to make 
  // the servo slow down or speed up. Note that the servo can't
  // move faster than its full speed, and you won't be able
  // to update it any faster than every 20ms.

  // Tell servo to go to 180 degrees, stepping by two degrees
 /*
  for(position = 0; position < 180; position += 2)
  {
    servo1.write(position);  // Move to next position
    delay(20);               // Short pause to allow it to move
  }

  // Tell servo to go to 0 degrees, stepping by one degree

  for(position = 180; position >= 0; position -= 1)
  {                                
    servo1.write(position);  // Move to next position
    delay(20);               // Short pause to allow it to move
  }*/
}

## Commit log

2016-07-01 new repo's ''rebase''
    [11in_barbie_mower.scad, Digikey_ShopCart.xls, LTC6803 breakout.brd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]
2016-07-08 Added Layla parts list and BMS operation summary.
    [Layla_parts_list.xlsx, RobotMoose_BMS_Operation.xlsx]
2016-07-08 Basic frame of Layla finished, sketches on top and bottom plywood pieces show dimensions and bracket placement.
    [11in_barbie_mower.SLDPRT, Conduit_Back.SLDPRT, Conduit_Front.SLDPRT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]
2016-07-09 More complete version of frame, with volcanos changed to 7 degrees.
    [Axle_7_16.SLDPRT, Camera_Bracket.SLDPRT, Conduit_Front.SLDPRT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]
2016-07-09 Remove junk
    [Part2.ipt, frame_bracket_volcano.SLDPRT, frame_bracket_volcano_left.SLDPRT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]
2016-07-09 Move stuff up.
    [11in_barbie_mower.SLDPRT, Axle_7_16.SLDPRT, Camera_Bracket.SLDPRT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]
2016-07-09 Added caster wheel.
    [Caster Part.SLDPRT, Layla.SLDASM, Layla_Bottom.SLDPRT]
2016-07-09 Added lots of screws to the assembly.
    [Layla.SLDASM, SCREW_8-FH(0.500'').SLDPRT, SCREW_8-FH(0.750'').SLDPRT]
2016-07-10 Reorganized slam code and added code for distributed particle slam.
    [config.txt]
2016-07-11 Increase size of wiring hole in wallplate, to leave room for steel charge plate tabs.
    [charge_wallplate.scad]
2016-07-13 Layla mostly complete, just missing some buttons and wiring.
    [10 PORT HEADER.SLDPRT, 102 RESISTOR PACK.SLDPRT, 103 RESISTOR PACK.SLDPRT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]
2016-07-15 Added schematics and exploded views for Layla construction.
    [Charge_Plate.SLDPRT, Charger.SLDASM, Counterweight_Ingot_Screw.SLDPRT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]
2016-07-19 Added version of charger that is a solid piece...
    [charger_front_v3.stl]
2016-07-23 Added solidworks and STL files for 1/8th scale Layla.
    [Camera_Print.STL, Camera_Print.sldprt, Caster_Print.SLDPRT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]
2016-08-02 Added simple white noise filter to stabilize the DOA, and switched from using median angle to average angle.
2016-08-02 Created bracket to attach Kinect to Layla in current place of webcam.
    [Kinect360_Mount_Bottom.SLDPRT, Kinect360_Mount_Top.sldprt]
2016-08-26 Adding Robot Arm scad and stl files.
    [Top_of_wrist_box.stl, arm_body.scad, bottom_arm_attach_piece.stl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]
2016-08-26 Adding Arduino servo code.
2016-09-01 Added kinect mount, removed sound localize since more recent version is on software git.
    [Kinect360_Mount_Top.sldprt, Kinect_Plate.SLDPRT, Wide_BandPass.dsn]
2017-04-17 Added roomba frame brackets.
    [Roomba_CornerBracket_180.stl, Roomba_CornerBracket_90.stl, roomba_laptop_front_corner_bracket.STL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]
2017-04-24 added telescoping pole mounts
    [pvc_0.75in_id_pipe.stl, pvc_tele_15.2.stl, pvc_tele_19.2.stl]
2018-02-16 Better roomba frame bracket.
    [roomba_CornerBracket_Mk2.SLDPRT, roomba_CornerBracket_Mk2.STL]
2019-09-29 Add printable STL files for LAYLA parts.
    [axle_bracket.scad, axle_bracket.stl, motor_bracket.stl]
2019-09-29 Move LAYLA model into layla/parts directory.
    [Camera_Print.STL, Camera_Print.sldprt, Caster_Print.SLDPRT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]

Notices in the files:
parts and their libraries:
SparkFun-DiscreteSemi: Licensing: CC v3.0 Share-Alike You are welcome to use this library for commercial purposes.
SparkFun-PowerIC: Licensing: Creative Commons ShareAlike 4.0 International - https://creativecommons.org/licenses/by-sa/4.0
